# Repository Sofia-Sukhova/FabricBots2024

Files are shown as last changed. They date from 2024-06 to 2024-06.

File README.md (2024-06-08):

# FabricBots2024 :turtle:

## Команда

* [Бочкарев Федор](https://t.me/Ger0r0r)

* [Курицына Кристина](https://t.me/k_kriiis)

* [Каплун Тамара](https://t.me/Sbighev)

* [Бочкарева Софья](https://t.me/Sofa_Sukhova)

## Задача
```sh
Построить робота без колес с дистанционным управлением для прохождения полосы препятствий на время
```
## Решение

Шагающий робот. Основной механизм состоит из зубчатой передачи для 4-х ног и двух моторов коллекторного типа (на правую и левую пару соответственно). В каждой паре между ногами сохраняется разность фаз $\pi$/2 за счет первоначальной сборки. Между правой и левой парой разность фаз не сохраняется. Дополнительной точной опоры по необходимости служит специально заниженное основание корпуса. Управление осуществляется с пульта с помощью радиомодулей.

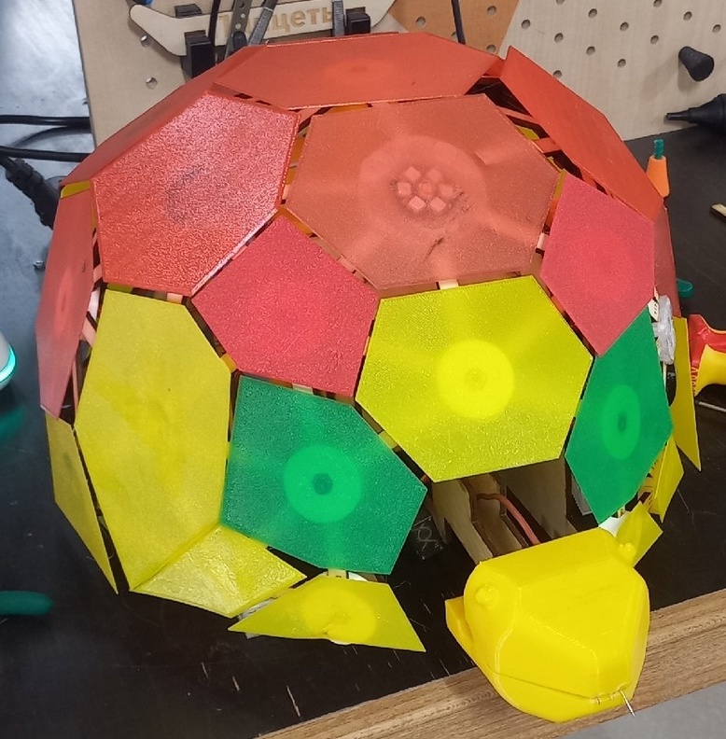
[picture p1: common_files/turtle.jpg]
Робот-черепаха




## Материалы и технологии

### Робот
- Основной корпус и оси ног выполнены из фанеры с помощью технологии лазерной резки СО_2 лазером
- Шестерни механизма, обшивка и голова робота напечатаны из PETG пластика на 3d принтере
- Основания ног и крепежные кольца для панциря напечатаны из TPU пластика на 3d принтере
- Модуль управления выполнен на основе
  - Arduino Uno
  - платы-драйвера управления моторами
  - двух коллекторных моторов
  - радиомодуля с антенной
  - светодиодной матрицы (7 светодиодов)
  - батарейного отсека (аккумуляторы 18650 х3)
  - тумблера управления питанием

### Пульт Управления
- Корпус пульта выполнен из фанеры с помощью технологии лазерной резки СО_2 лазером
- Модуль управления выполнен на основе
  - Arduino Pro Micro
  - джойстика (управление движением робота)
  - тумблера и кнопки (управление светодиодной матрицей)
  - радиомодуля с антенной

## Трудности и проблемы

### Механизм

Изначально мы изготовили зубчатую передачу на основе деревянных шестерней, свободно вращающихся на оси, с передаточным числом механизма M=1. Оказалось, что при таких условиях механизму не хватает момента и мощности (из-за значительного трения между шестернями) для передвижения. 

Поэтому мы изменили механизм для достижения передаточного числа M=5, выполнили шестерни из PETG и закрепили их с помощью подшипников.

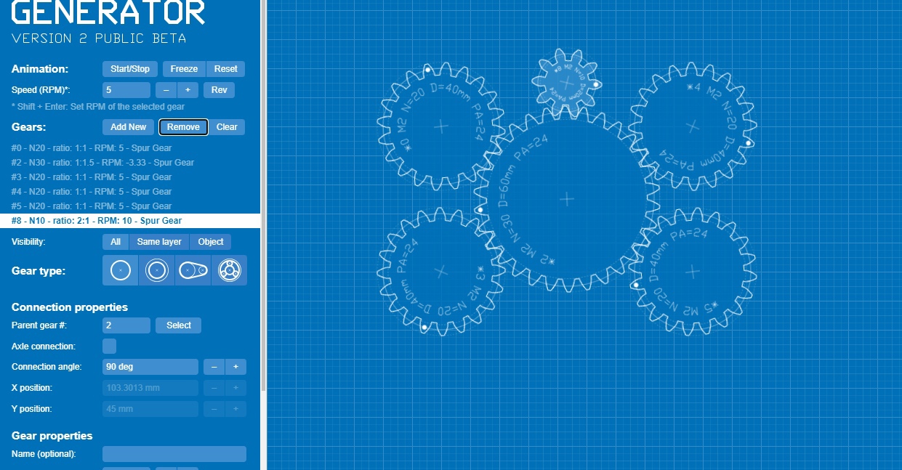
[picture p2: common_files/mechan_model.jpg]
Модель зубчатой передачи

*Примерный вид механизма, реальные диаметры шестерней 10, 50 (х4) и 70 мм*

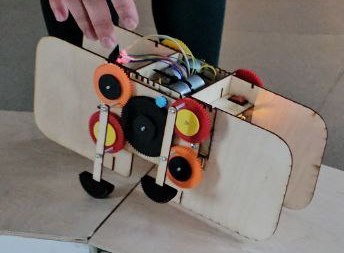
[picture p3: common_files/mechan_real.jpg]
Реализация механизма


### Корпус

Основной трудностью при изготовлении корпуса было учесть все особенносьти робота (размеры, необходимоть дополнительной опоры, крепление мехнанизма, размещение управляющих элеметов), из-за чего пришлось несколько раз полностью перепроектировать основной корпус.

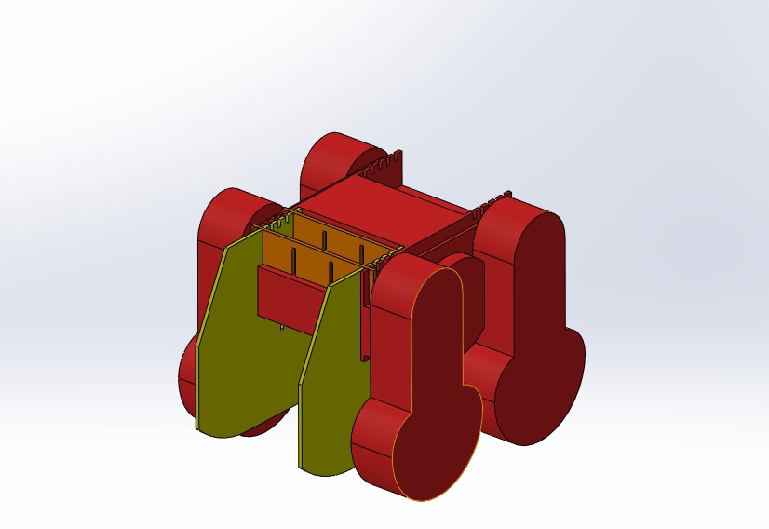
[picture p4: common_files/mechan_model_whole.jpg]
Полная модель корпуса


В качестве дизайна робота была выбрана черепаха. Поэтому у нас также возникла трудность проектирования и изготовления панциря из плоских составных деталей и его крепления к основному корпусу.

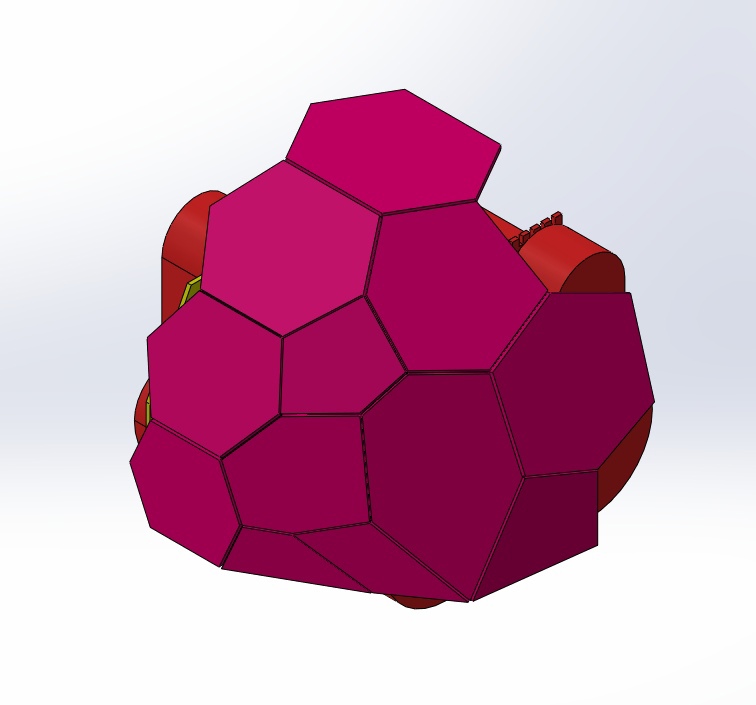
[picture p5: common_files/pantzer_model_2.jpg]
Модель панциря


### Управление

В процессе работы платы управления и радиомодулей несколько раз выходили из строя, что приводило к необходимости полной перепайки управляющей схемы.

Также возникли трудности с настройкой радиомодуля, для чего потребовалось создать многочисленные скетчи анализа подключения/работы радиомодуля.

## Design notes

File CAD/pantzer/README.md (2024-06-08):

При изготовлении панциря необходимо тщательно сделать за правильностью и количеством деталей

На [картинке](https://github.com/Sofia-Sukhova/FabricBots2024/blob/main/CAD/pantzer/pantzer.jpg) представлена нумерация пластин, соответствующая 3mf файлам. Нужно проверять количество и симметрию напечатанных пластин.

Крепление осуществляется с помощью упругих вершин (весь набор в [fasteners_full.3mf](https://github.com/Sofia-Sukhova/FabricBots2024/blob/main/CAD/pantzer/fasteners_full.3mf)) и деревянных ребер ([CorelDraw/fasteners_for_pantzer](https://github.com/Sofia-Sukhova/FabricBots2024/blob/main/CorelDraw/fasteners_for_pantzer.cdr) - полный набор), поэтому печать вершин нужно делать из TPU (кроме центрального крепления), и также следить за количеством/ симметрией

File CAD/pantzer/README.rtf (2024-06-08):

При изготовлении панциря необходимо тщательно сделать за правильностью и количеством деталей

На картинке представлена нумерация пластин, соответствующая 3mf файлам. Нужно проверять количество и симметрию напечатанных пластин.

Крепление осуществляется с помощью упругих вершин (весь набор в fasteners_full.3mf) и деревянных ребер (CorelDraw/stiks - полный набор), поэтому печать вершин нужно делать из TPU (кроме центрального крепления), и также следить за количеством/ симметрией

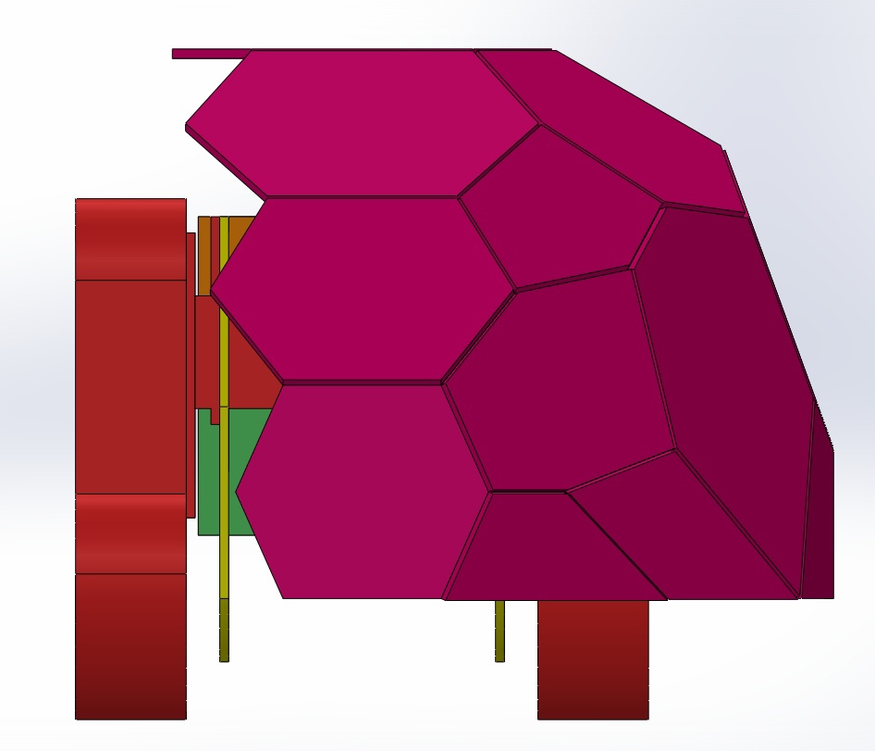
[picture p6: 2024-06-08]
common_files/pantzer_model.jpg

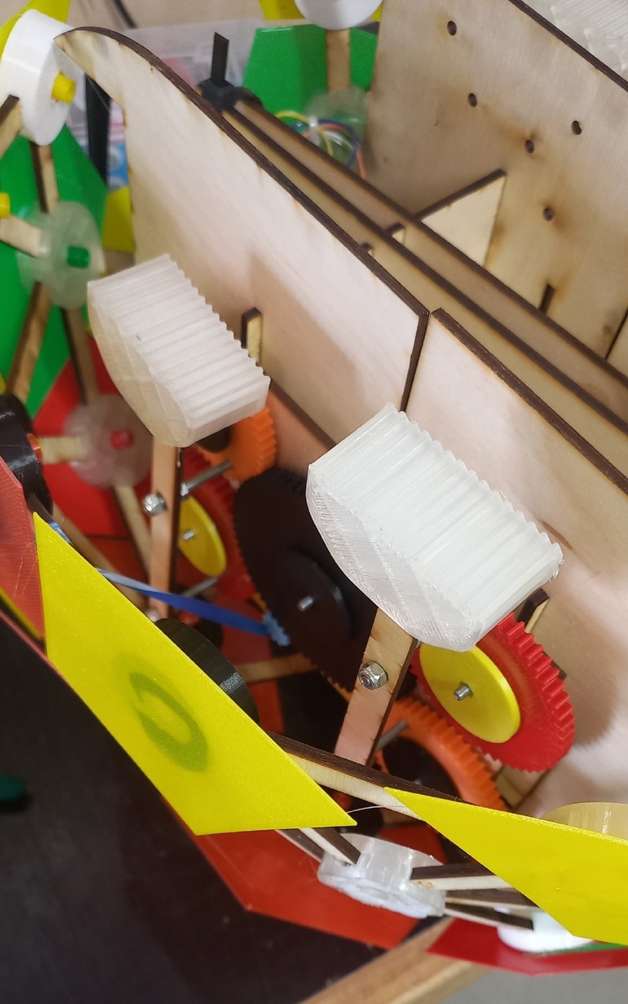
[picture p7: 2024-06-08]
common_files/legs_view.jpg

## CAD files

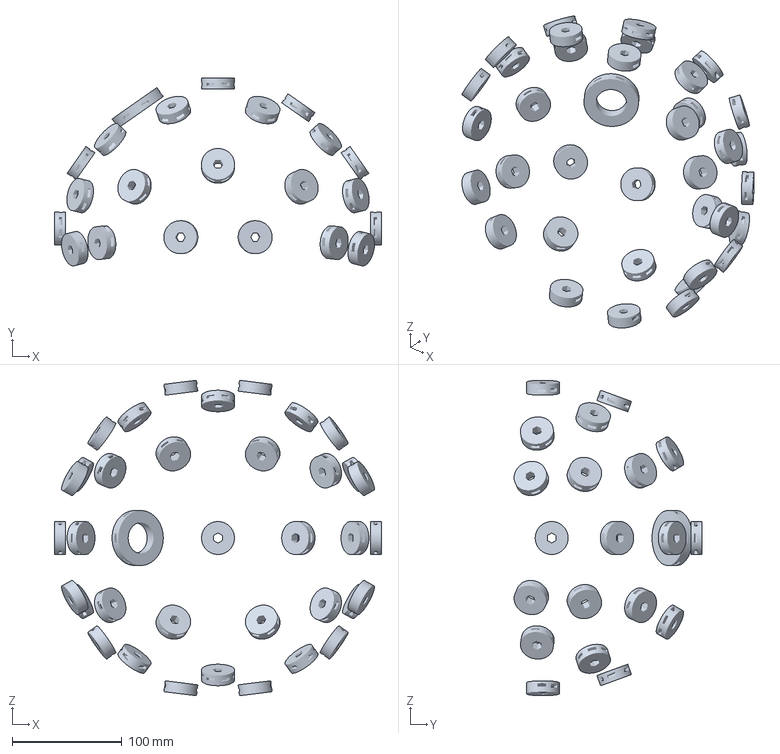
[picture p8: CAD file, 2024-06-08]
CAD/pantzer/fasteners_full.3mf
298.0 x 171.2 x 287.5 mm

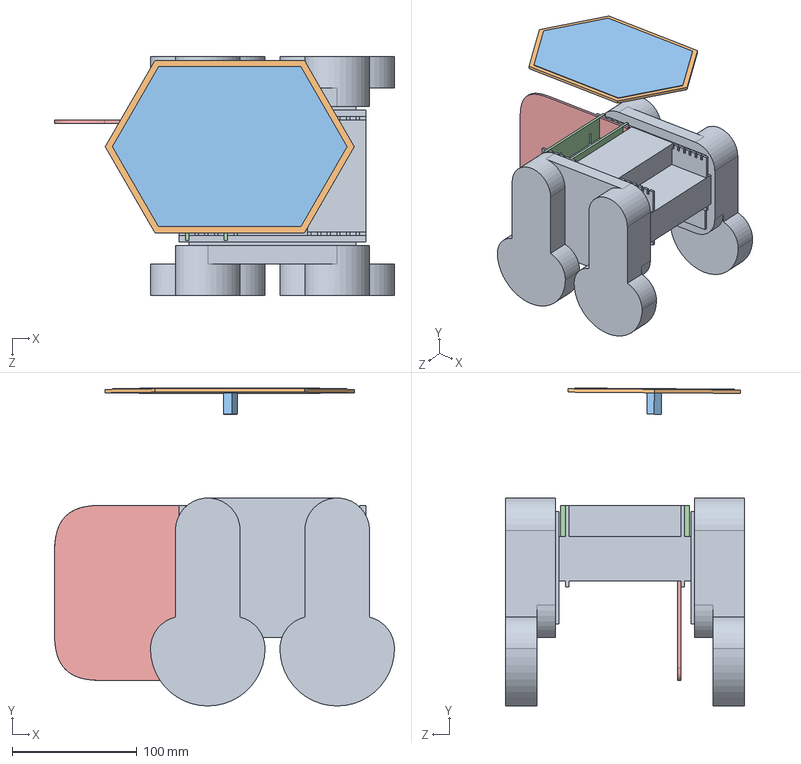
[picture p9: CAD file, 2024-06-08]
CAD/pantzer/Сборка.SLDASM
273.0 x 255.3 x 191.6 mm
Механизм (как целое)
Верхняя плита дерево
Верхняя плита пластик
Верхняя поперечная балка x 2
Полозья

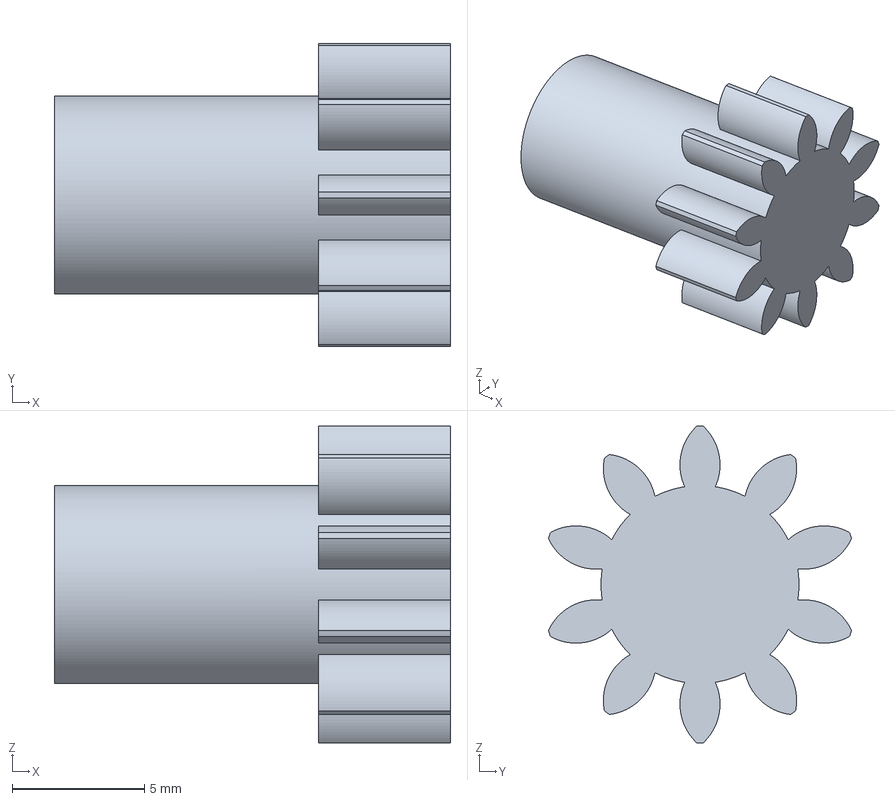
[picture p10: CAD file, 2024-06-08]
CAD/gears/Shesternya_10_privod.3mf
15.0 x 11.5 x 12.0 mm

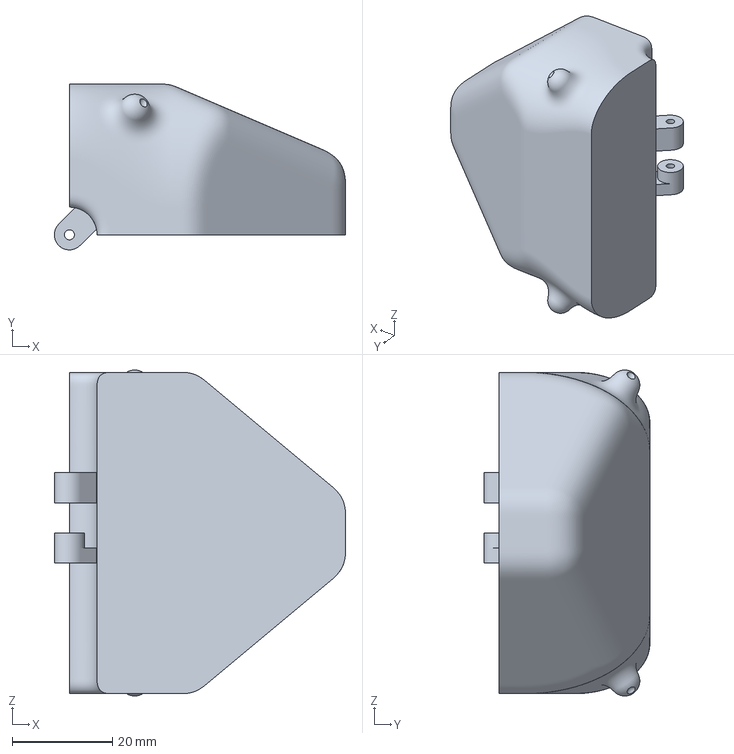
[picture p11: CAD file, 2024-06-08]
CAD/head/Verkhnyaya_chelyust_novaya.3mf
58.0 x 33.0 x 64.9 mm

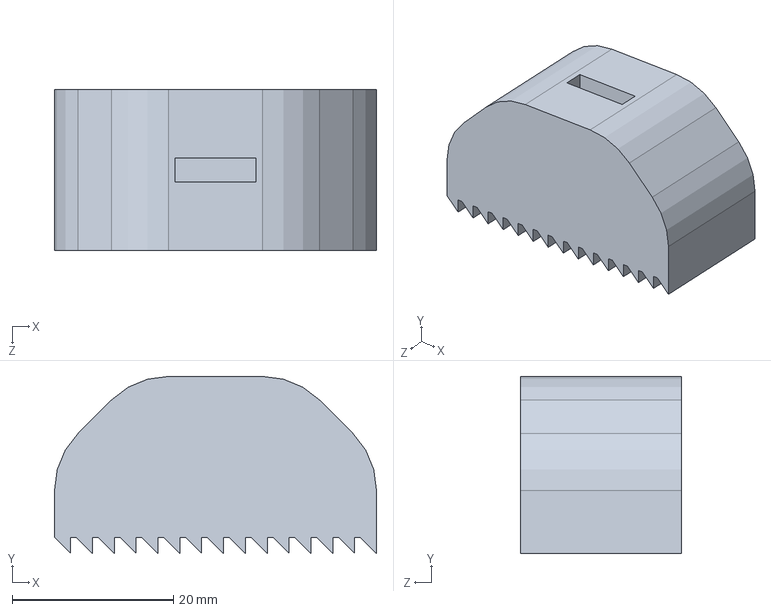
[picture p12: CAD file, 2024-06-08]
CAD/legs/foot.SLDPRT
40.0 x 22.0 x 20.0 mm

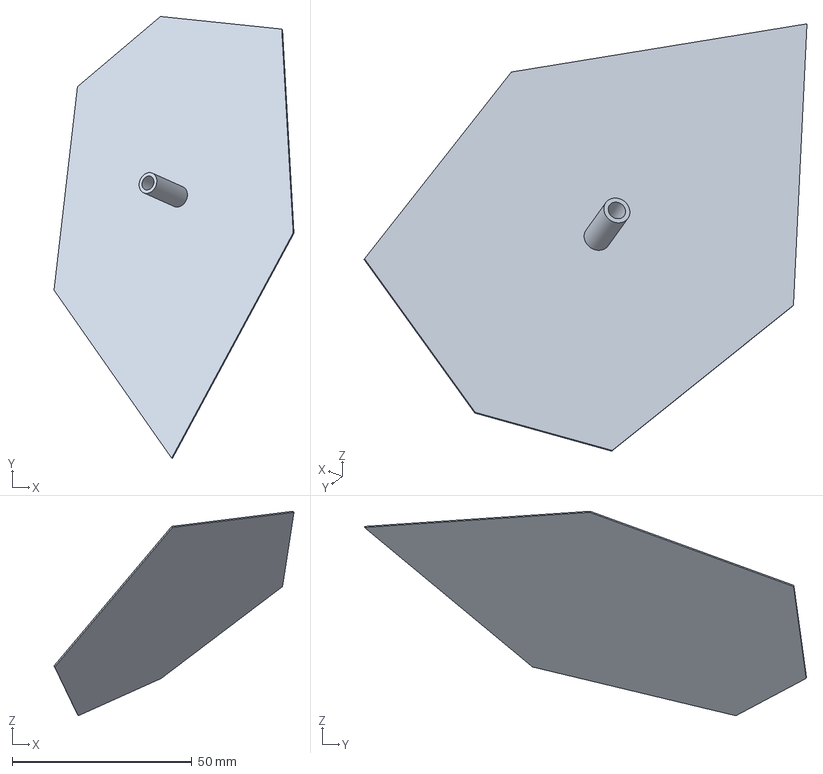
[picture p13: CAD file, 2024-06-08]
CAD/pantzer/Pantsir_10.3mf
66.8 x 123.0 x 56.9 mm

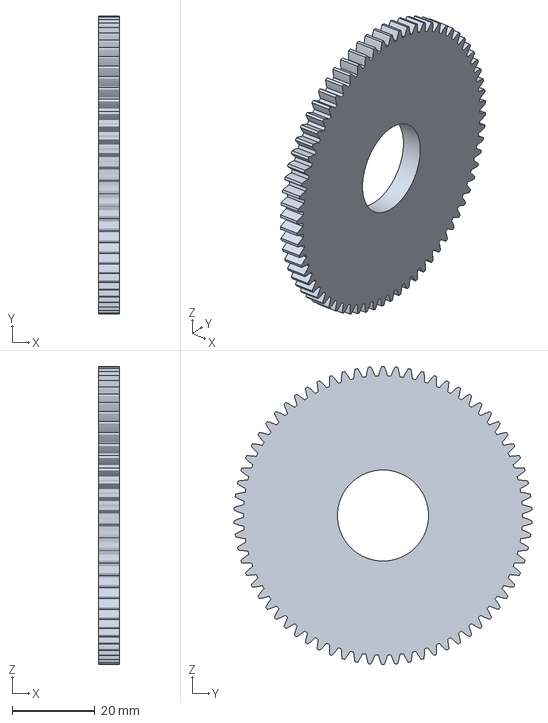
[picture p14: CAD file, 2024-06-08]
CAD/gears/Shesternya_70_22_mm_val.3mf
5.00 x 72.0 x 72.0 mm

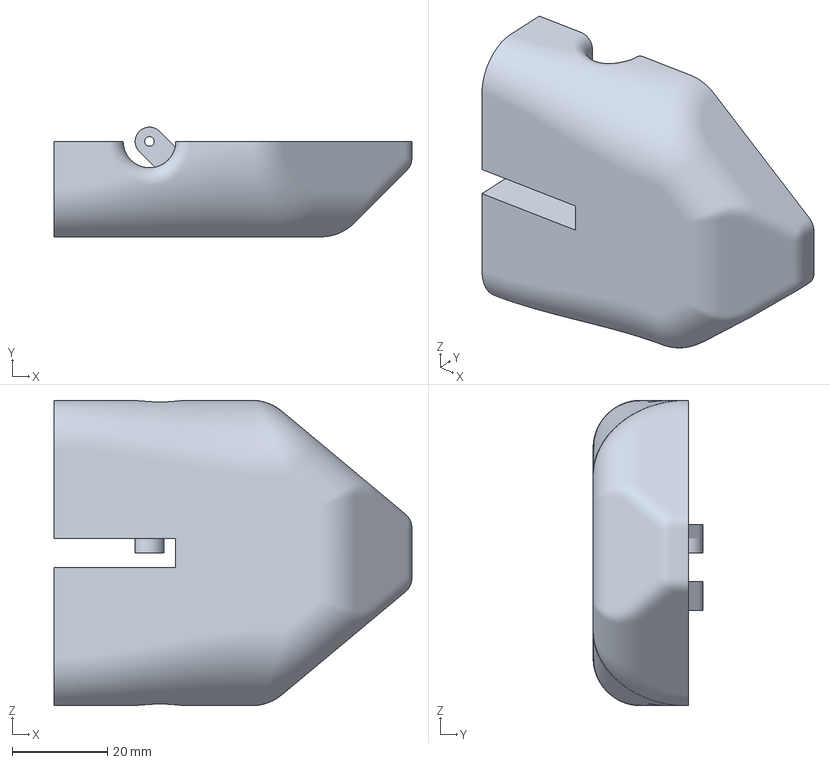
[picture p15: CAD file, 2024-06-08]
CAD/head/Nizhnyaya_chelyust_novaya.3mf
75.0 x 23.0 x 64.0 mm

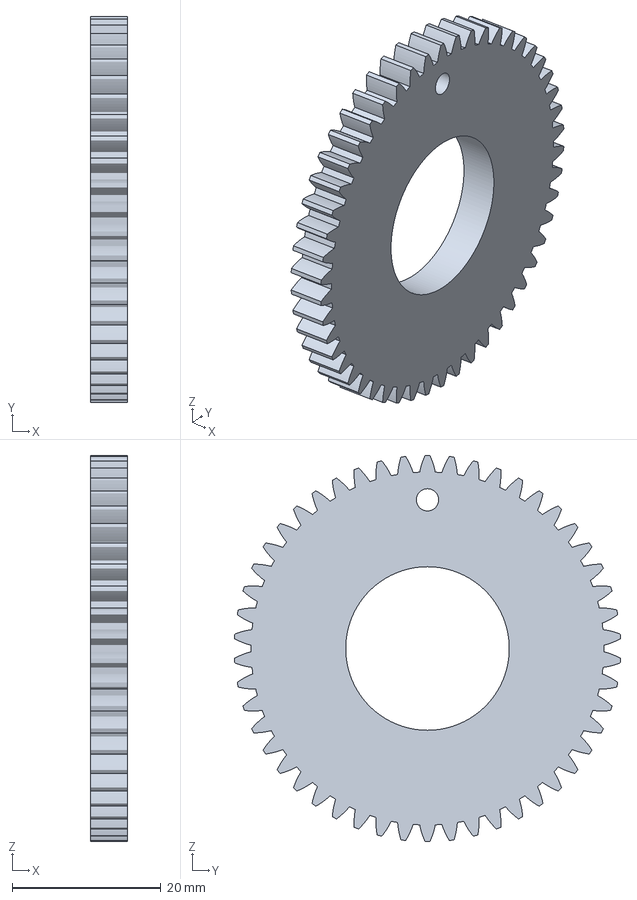
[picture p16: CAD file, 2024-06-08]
CAD/gears/Shesternya_50_22_mm_val.3mf
5.00 x 51.9 x 52.0 mm

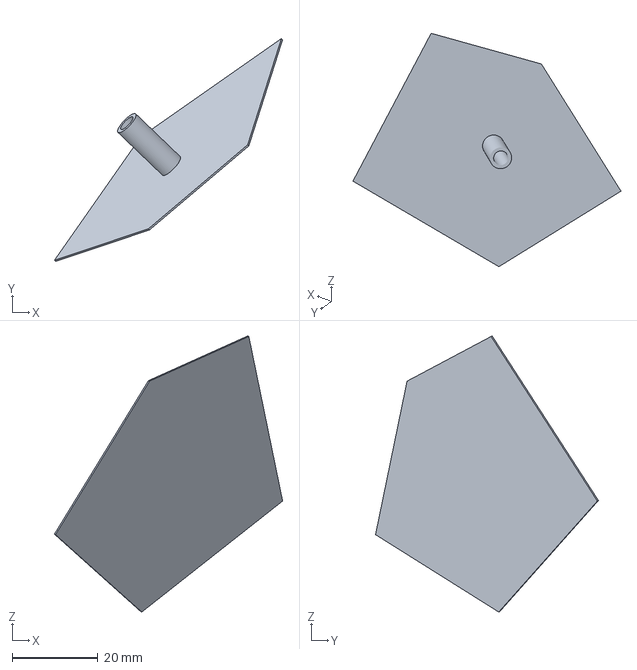
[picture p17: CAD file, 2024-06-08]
CAD/pantzer/Pantsir_06.3mf
53.1 x 51.9 x 64.2 mm

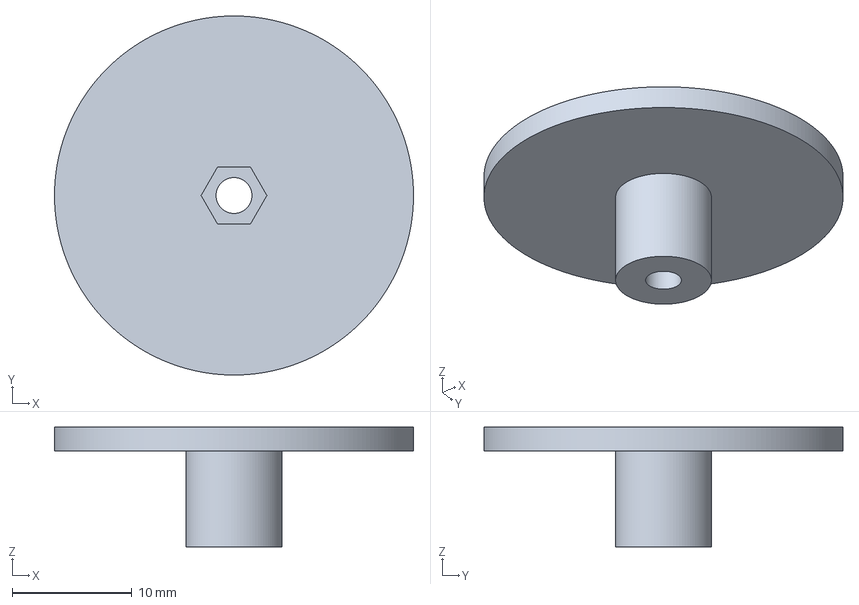
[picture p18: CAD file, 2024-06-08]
CAD/gears/Val_podshipnika.3mf
30.0 x 30.0 x 10.0 mm

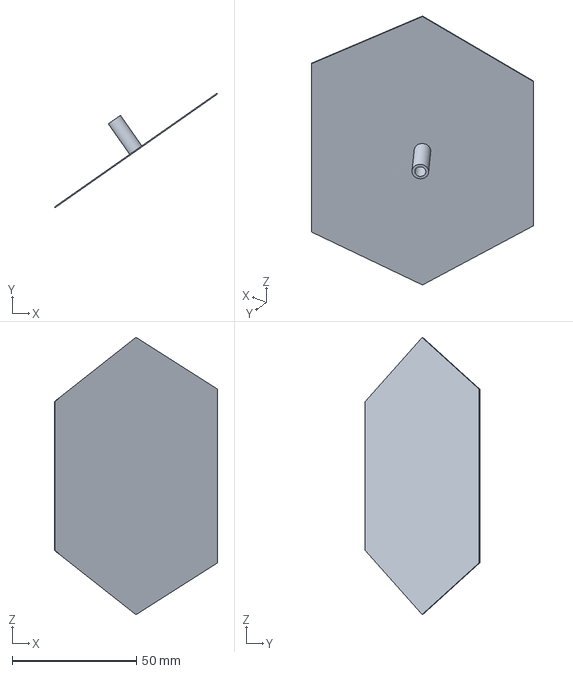
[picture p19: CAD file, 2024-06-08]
CAD/pantzer/Pantsir_02.3mf
65.8 x 46.2 x 111.6 mm

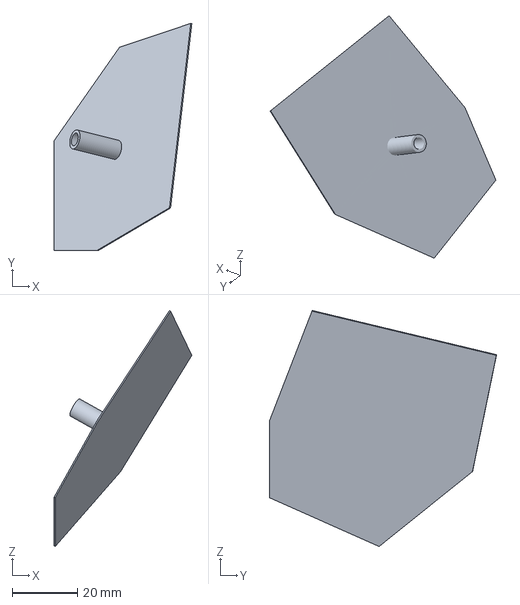
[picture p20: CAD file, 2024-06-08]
CAD/pantzer/Pantsir_07.3mf
42.3 x 69.8 x 72.5 mm

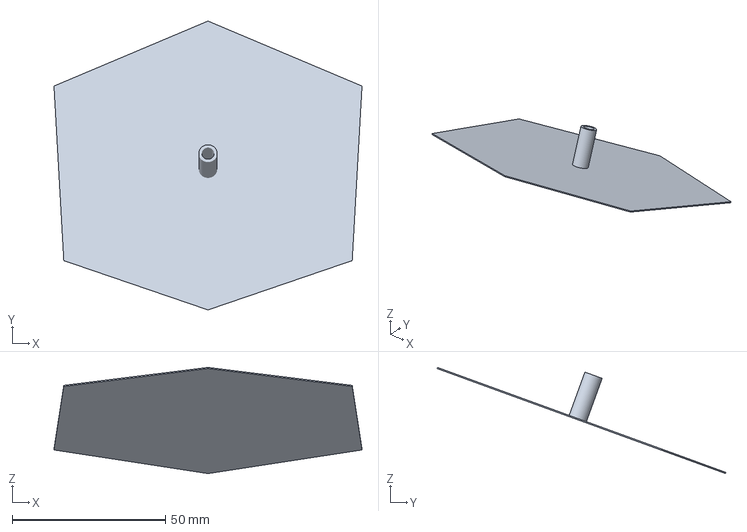
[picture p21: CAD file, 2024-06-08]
CAD/pantzer/Pantsir_09.3mf
100.3 x 94.1 x 34.6 mm

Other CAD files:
CAD/pantzer/Pantsir_05_l.3mf
CAD/pantzer/Pantsir_12.3mf
CAD/pantzer/Pantsir_03.3mf
CAD/pantzer/Pantsir_11.3mf
CAD/legs/foot.3MF
CAD/pantzer/Pantsir_01.3mf
CAD/pantzer/Pantsir_05.3mf
CAD/pantzer/Pantsir_08.3mf

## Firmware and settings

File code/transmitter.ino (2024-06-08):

#include <SPI.h>
#include <nRF24L01.h>
#include <RF24.h>

#define DEBUG 0
#define TICKRATE 1
#define LOG DEBUG || TICKRATE

RF24 radio(9, 10);
int data[5];  

const int xPin = A0;
const int yPin = A1;
const int buttonPin = 4;
const int ptmrPin = A2;
const int tumblrPin = 6;

int xPosition = 0;
int yPosition = 0;
#define POS_DELTA 25
#define POS_STOP 150

int buttonState = 0;
int tumblrState = 0;
int ptmrState = 0;

int position = 4;
int speed = 0;
int direction = 0;
                                
void setup(){
    radio.begin();
    radio.setChannel(100); // Channel (from 0 to 127), 5 - freq 2,405 GHz (only 1 receiver on a single channel and up to 6 transmitters)
    radio.setDataRate     (RF24_1MBPS); // Speed (RF24_250KBPS, RF24_1MBPS, RF24_2MBPS)
    radio.setPALevel      (RF24_PA_HIGH); // Transmitter power (RF24_PA_MIN=-18dBm, RF24_PA_LOW=-12dBm, RF24_PA_HIGH=-6dBm, RF24_PA_MAX=0dBm)
    radio.openWritingPipe (0x1234567890LL); 
    #if LOG
    Serial.begin(115200);
    #endif
    pinMode(xPin, INPUT);
    pinMode(yPin, INPUT);
    pinMode(buttonPin, INPUT_PULLUP);
    pinMode(tumblrPin, INPUT);
    pinMode(ptmrPin, INPUT);
}

#ifdef TICKRATE
#define M_TICK_SIZE 32

unsigned int tickrate[M_TICK_SIZE];
int i = 0;
unsigned int old_v, new_v;
unsigned int sum, max;
#endif

void loop(){
    xPosition = analogRead(xPin);
    yPosition = analogRead(yPin);
    buttonState = digitalRead(buttonPin);
    tumblrState = digitalRead(tumblrPin);
    ptmrState = analogRead(ptmrPin);

    #if DEBUG
    Serial.println("");
    Serial.println("");
    Serial.print("x\t");
    Serial.println(xPosition);
    Serial.print("y\t");
    Serial.println(yPosition);
    Serial.print("btn\t");
    Serial.println(buttonState);
    Serial.print("tmb\t");
    Serial.println(tumblrState);
    Serial.print("ptr\t");
    Serial.println(ptmrState);
    #endif

    xPosition -= 512;
    yPosition -= 512;

    position = ((abs(xPosition) - abs(yPosition)) > POS_DELTA) ? xPosition : ((abs(yPosition) - abs(xPosition)) > POS_DELTA) ? yPosition : position;
    direction = ((abs(xPosition) - abs(yPosition)) > POS_DELTA) ? 2 : ((abs(yPosition) - abs(xPosition)) > POS_DELTA) ? 0 : direction;
    direction += (position > 0) ? 0 : 1;

    bool flag = (abs(xPosition) < POS_STOP && abs(yPosition) < POS_STOP);

    direction = (flag) ? 4 : direction;
    speed = (flag) ? 0 : map(abs(position), 0, 512, 0, 255);
    
    #if DEBUG
    Serial.print("pos\t");
    Serial.println(position);
    Serial.print("speed\t");
    Serial.println(speed);
    Serial.print("dir\t");
    Serial.println(direction);
    #endif

    data[0] = direction;
    data[1] = speed;
    data[2] = !buttonState;
    data[3] = tumblrState;
    data[4] = ptmrState;
    radio.write(&data, sizeof(data)); // check delivery: if(radio.write(&data, sizeof(data)))

    #if TICKRATE
    new_v = millis();

    sum -= tickrate[i];
    tickrate[i] = new_v - old_v;
    sum += tickrate[i];
    max = 0;
    for (int j = 0; j < M_TICK_SIZE; j++) {
      max = (tickrate[j] > max) ? tickrate[j] : max;
    }
    
    i = (i == 31) ? 0 : i + 1;
    Serial.println("");
    Serial.print("Tickrate\t");
    Serial.println((float)sum / M_TICK_SIZE);
    Serial.print("Max ping\t");
    Serial.println(max);
    old_v = new_v;
    #endif
}

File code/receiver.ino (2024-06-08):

#include <SPI.h>
#include <nRF24L01.h>
#include <RF24.h>
#include <Adafruit_NeoPixel.h>
#ifdef __AVR__
 #include <avr/power.h> // Required for 16 MHz Adafruit Trinket
#endif

#define DEBUG 0
#define TICKRATE 1
#define LOG DEBUG || TICKRATE

#define SPEED_1 5
#define DIR_1 4

#define SPEED_2 6
#define DIR_2 7

#define MATRIX_PIN 10
#define LED_COUNT 7
#define MAX_BRIGHTNESS 255

Adafruit_NeoPixel matrix(LED_COUNT, MATRIX_PIN, NEO_GRB + NEO_KHZ800);

RF24 radio(8, 9);  // nRF24L01+ (CE, CSN)
int data[5];

void setup() {

#if defined(__AVR_ATtiny85__) && (F_CPU == 16000000)
  clock_prescale_set(clock_div_1);
#endif
  #if LOG
  Serial.begin(115200);
  #endif

  radio.begin();
  radio.setChannel(100);
  radio.setDataRate(RF24_1MBPS);
  radio.setPALevel(RF24_PA_HIGH);
  radio.openReadingPipe(1, 0x1234567890LL);
  radio.startListening();
  //  radio.stopListening ();

  // motor pins
  for (int i = 4; i < 8; i++) {
    pinMode(i, OUTPUT);
  }

  matrix.begin();
  matrix.setBrightness(MAX_BRIGHTNESS);
}

int btnState;
int tmblrState;
int ptmrVal;

#ifdef TICKRATE
#define M_TICK_SIZE 32

unsigned int tickrate[M_TICK_SIZE];
int i = 0;
unsigned int old_v, new_v;
unsigned int sum, max;
#endif

void loop() {

  if (radio.available()) {
    radio.read(&data, sizeof(data));

    #if DEBUG
    Serial.println("");
    Serial.println(data[0]);
    Serial.println(data[1]);
    Serial.println(data[2]);
    Serial.println(data[3]);
    Serial.println(data[4]);
    #endif
    
    btnState = data[2];
    tmblrState = data[3];
    ptmrVal = data[4];

    // 0 - Forward, 1 - backward, 2 - right, 3 - left
    switch (data[0]) {
      case 0:
        {
          digitalWrite(DIR_1, HIGH);  // set direction
          analogWrite(SPEED_1, 255);  // set speed

          digitalWrite(DIR_2, HIGH);
          analogWrite(SPEED_2, 0);

          break;
        }
      case 1:
        {
          digitalWrite(DIR_1, LOW);
          analogWrite(SPEED_1, 0);

          digitalWrite(DIR_2, LOW);
          analogWrite(SPEED_2, 255);

          break;
        }
      case 2:
        {
          digitalWrite(DIR_1, HIGH);
          analogWrite(SPEED_1, 255);

          digitalWrite(DIR_2, LOW);
          analogWrite(SPEED_2, 255);

          break;
        }
      case 3:
        {
          digitalWrite(DIR_1, LOW);
          analogWrite(SPEED_1, 255);

          digitalWrite(DIR_2, HIGH);
          analogWrite(SPEED_2, 255);

          break;
        }
      case 4:
        {
          analogWrite(SPEED_1, 0);
          analogWrite(SPEED_2, 0);

          break;
        }
    }
  }

  matrix.clear(); // Set all pixel colors to 'off'
  if (!tmblrState) {
      Serial.println("LoL 1");
    if (!btnState) {
      Serial.println("LoL 2");
      matrix.fill(matrix.Color(255, 255, 255), 0, 7);
    } else {
      Serial.println("LoL 3");
      matrix.fill(matrix.Color(50, 50, 50), 0, 7);
    }
  } else {
    matrix.fill(matrix.Color(0, 0, 0), 0, 7);
  }
  matrix.show();
  
  #if TICKRATE
    new_v = millis();

    sum -= tickrate[i];
    tickrate[i] = new_v - old_v;
    sum += tickrate[i];
    max = 0;
    for (int j = 0; j < M_TICK_SIZE; j++) {
      max = (tickrate[j] > max) ? tickrate[j] : max;
    }
    
    i = (i == 31) ? 0 : i + 1;
    Serial.println("");
    Serial.print("Tickrate\t");
    Serial.println((float)sum / M_TICK_SIZE);
    Serial.print("Max ping\t");
    Serial.println(max);
    old_v = new_v;
    #endif
}
